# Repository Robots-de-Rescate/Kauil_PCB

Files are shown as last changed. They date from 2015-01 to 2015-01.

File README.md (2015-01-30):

This repository contains the design files for the PCB found on Kauil. The main motivation behind the desigh of this PCB is to have a platform for testing and implementing new hardware easily. Also it should be easy for new students joining the team to start developing for it, this is why we choosed to use the same development board as a core as the one used in the microcontroller (embedded systems) class, the [STM32F3 discovery](http://www.st.com/web/catalog/tools/FM116/SC959/SS1532/PF254044).

The design files were made using [DipTrace](http://diptrace.com/) which can be downloaded freely for 30 days, or without time limitations but with a 300 pin limitation (this design contains more than 300 pins).

## Design of the PCB

The board is for the most part an interface to the various peripherals available on the STM32F3 microcontroller,
but there are also some specific functionalities that should be noted, the is a summary of what the PCB has:

+ Specific purpose connectors, 2 for the MD03 boards and 2 for the encoders. 
+ Driver circuit for a Buzzer to serve as a low battery alert.
+ Driver circuit to read a button so it can be used as an emergency stop. 
+ Analog multiplexer with a voltage divider to measure the voltage of all 5 batteries connected, plus 2 optional
  external signals while using just one ADC.
+ 4 SPI connectors (2 of them 5V tolerant), two connectors per SPI peripheral from the microcontroller with the
  use of CS pins.
+ 4 I2C external connectors, one pair per I2C peripheral on the microcontroller. 2 of them are pulled up to 3.3V
  while the other two are pulled up to 5V.
+ USB communication directly from the microcontroller.
+ One connector for an I2C to USB interface in case communications get saturated over the microcontroler's USB 
  port.
+ 3D gyroscope, 3D magnetometer and 3D accelerometer provided by the STM32F3 discovery board.
+ 5 UART ports (4 of them 5V tolerant)
+ 4 ADC pins exposed to connectors to sense data from various sources.
+ All UART, I2C and SPI connectors have GND and power pins according to the supported voltage to ease the 
  connection of devices with just one connector and one cable.
+ Almost any pin can be set to be a GPIO pin if its specific functionality is not required.

The following diagram shows which pins from the microcontroller are connected to which components on the board,
it's also important to note the red ports that mark issues found while using the board and how they were fixed,
for more information on these see [Known-issues](#known-issues).

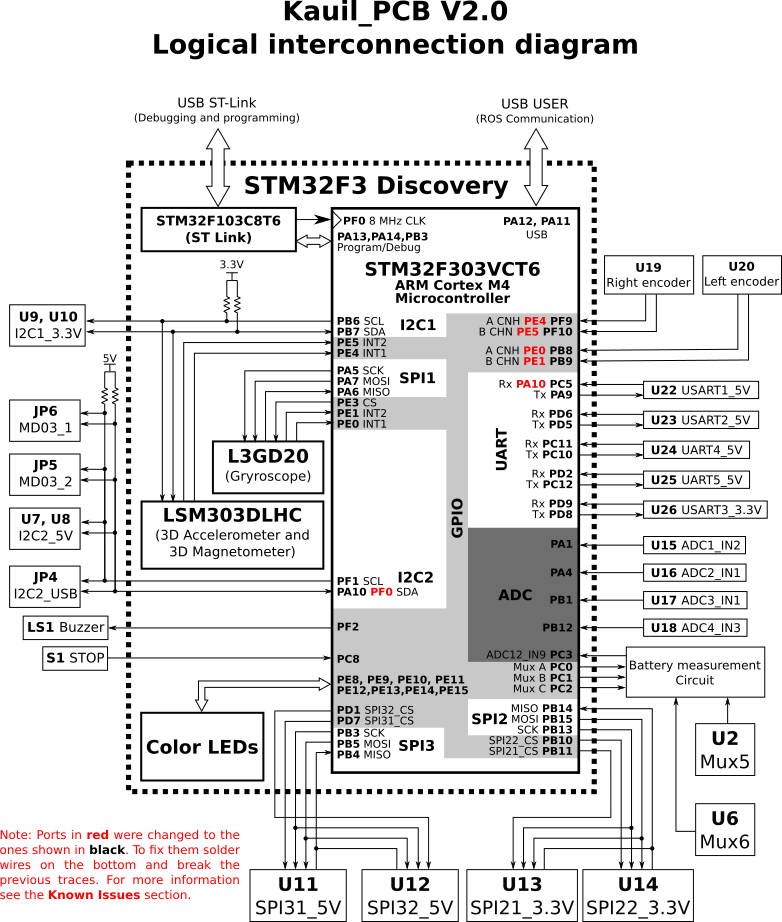
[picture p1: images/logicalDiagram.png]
Logic diagram
  
[PDF version](images/logicalDiagram.pdf)  
[Inkscape's svg version](images/logicalDiagram.svg)

The next diagram shows how the Power sources are distributed within the PCB, care was taken to separate the
regulators that power up the cameras because they are the components that consume the most power (after the CPU
which does not appear in the diagram because it has its own battery and is connected directly).

Note: We've noticed that sometimes when connecting the battery to the regulator in which the Hokuyo is connected 
the regulator shuts down maybe due to a high peak current at startup, most of the times disconnecting and
connecting the battery again fixes this.

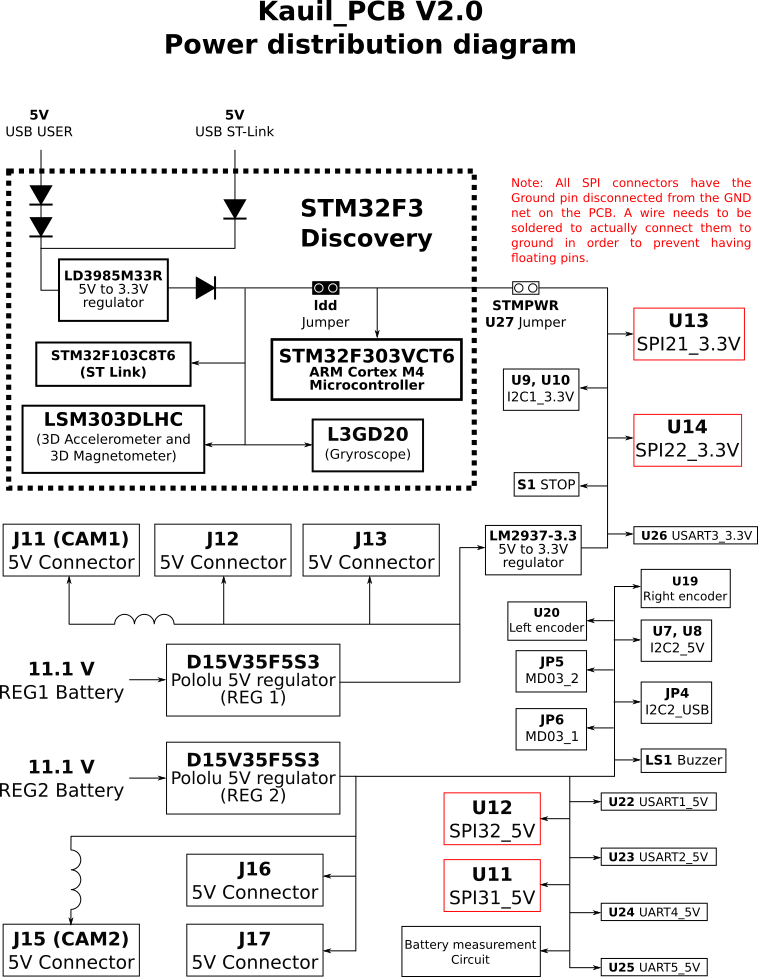
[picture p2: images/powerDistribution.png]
Power distribution
  
[PDF version](images/powerDistribution.pdf)  
[Inkscape's svg version](images/powerDistribution.svg)

To modify any of these diagrams clone the repository, edit the svg file locally with
[Inkscape](https://inkscape.org/), update the png and pdf versions and commit the changes.

## Content of the repository

+ **BOM:** This folder contains some spreadsheets with components used for the PCB, costs and suplier links.
+ **Gerbers:** This folder contains the files that were sent to the manufacturer to produce the actual PCB, they were exported from DipTrace.
+ **Lib:** This folder contains library files for DipTrace with all schematic components and PCB patterns used on the PCB, we do not use any external library besides the one provided by DipTrace and the ones found here, so the design is portable.
+ **PCB.dip:** A DipTrace file with the PCB layout and routing.
+ **PCB.jpg:** A .jpg image of the PCB for quick reference without requiring DipTrace
+ **Schematic.dch:** A DipTrace file with the schematic for the PCB, it contains information about logical connections of the board.
+ **Schematic.jpg:** A .jpg image with the schematics used for the PCB, for easy acces for people that do not have DipTrace.

## Known issues:

V2 of the PCB is the one that was manufactured and is found on Kauil, while doing the code implementation of it we found several problems with the design that had to be corrected for the system to work, the following list explains them, and the fix that was applied, future versions of the board should have them permanently fixed.

* The SDA pin from I2C2 (Used for the MD03 boards) was previously located
  on pin PF0, but this pin is occupied by an 8MHz clock signal that comes
  from the STLink microcontroller on the STM32F3 discovery (U2) and can't
  be changed without slowing down the main microcontroller (the actual
  PF0 pin on the header of the Discovery board is not connected to the 
  microcontroller, and has to be enabled by the SB12 jumper). To fix this 
  the PCB was modified to connect what came into PF0 before to PA10, this 
  pin was the Rx pin for USART1 before, but if required it can be assigned 
  to PC5 which is used for the STLink but suldn't be much trouble while 
  running code (because STLink is just used for programming and debugging), 
  it's important to note that this last jumper wire hasn't been soldered yet.  
  (**Peripherals affected:** I2C2 (MD03), USART1 (Rx pin) )

* The A and B channels for both encoders were assigned incorrectly to pins
  on the STM32F3 that were being already used for interrupts on the two
  sensor chips the LSM303DLHC and the L3GD20, to leave these pins free 
  for future use we chose to move the encoders to other pins, changes made
  were:

      PE4 -> PF9
      PE5 -> PF10
      PE0 -> PB8
      PE1 -> PB9

  (**Periherals affected:** Encoders and external interrupts for sensors 
   LSM303DLHC and the L3GD20)

* The PCB has 4 SPI external connectors, the connector is supposed to 
  provide Ground and Voltage pins to easily connect any device to them,
  but sadly when the schematic was created the Ground pins were left
  unconnected to the actual ground trace. To fix this a wire has to be
  soldered on the bottom of the PCB so the ground is correctly connected.  
  (**Peripherals affected:** all SPI external connectors)

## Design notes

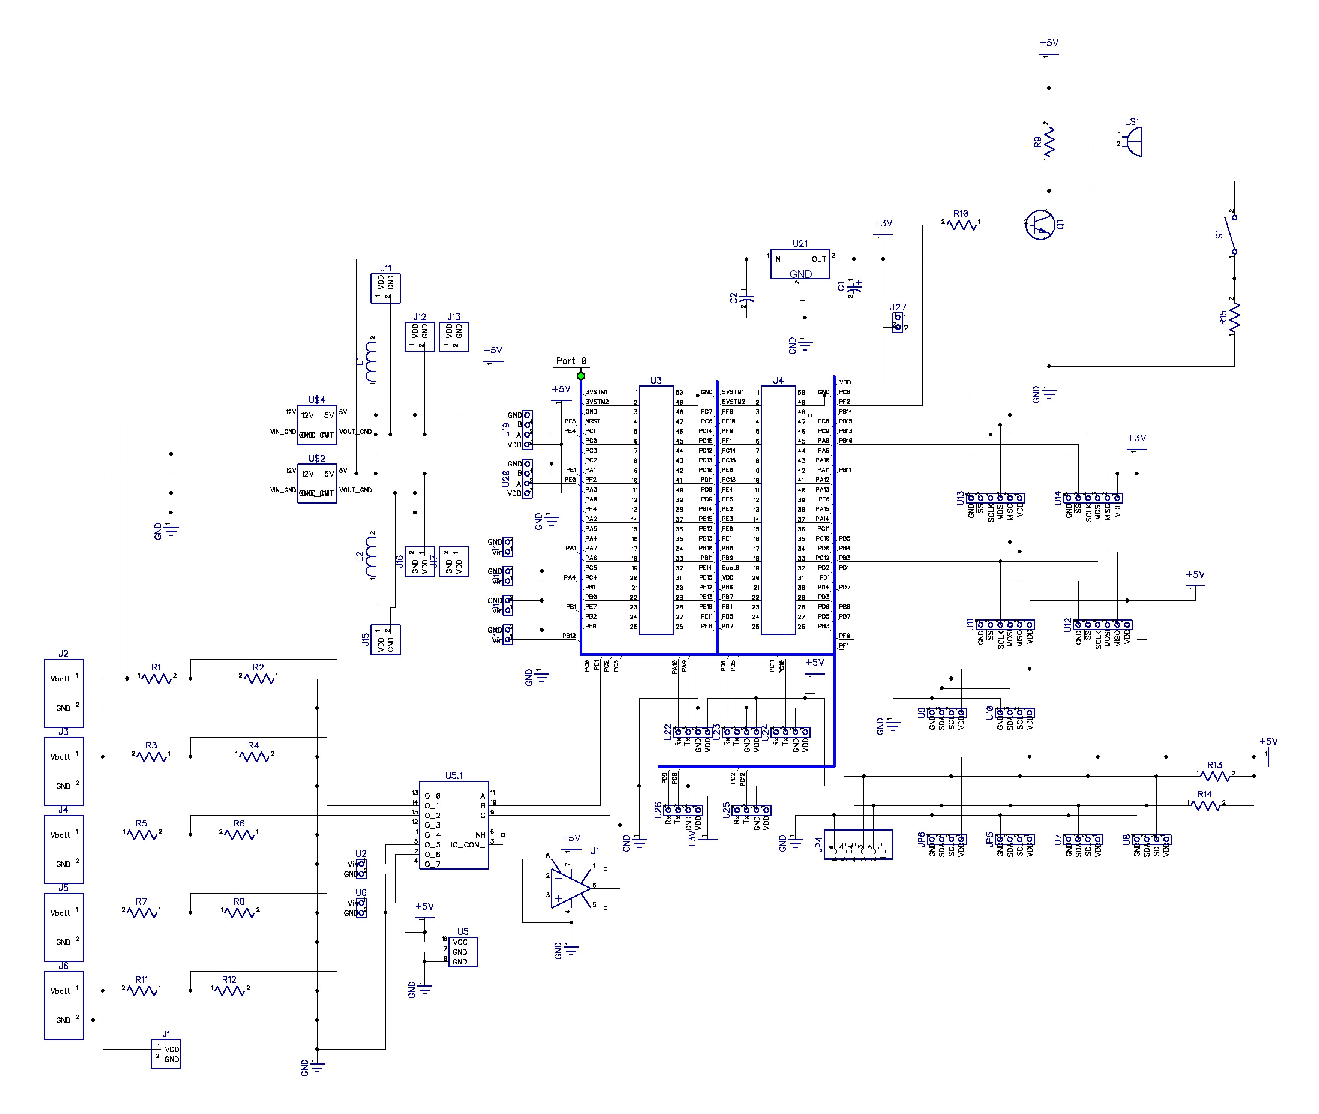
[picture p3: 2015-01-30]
Schematic.jpg

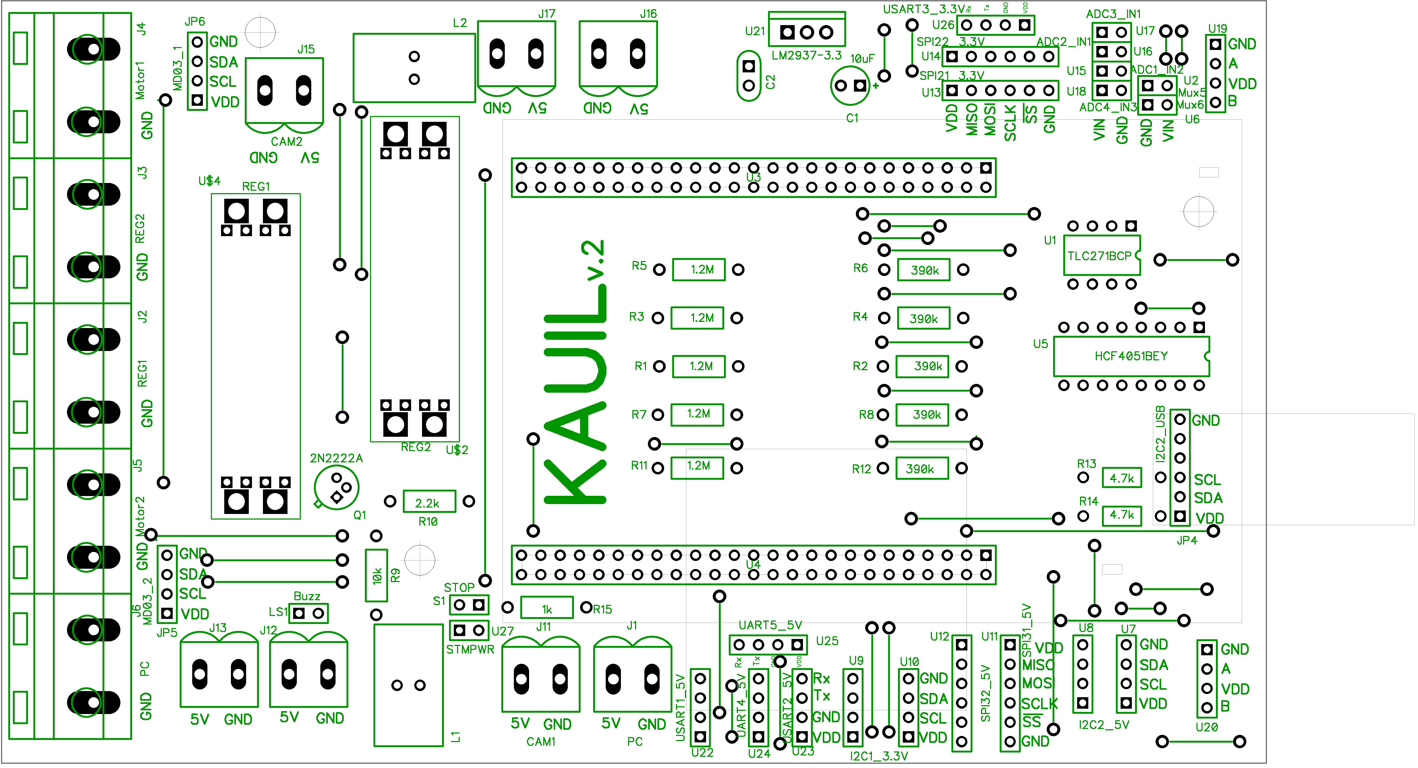
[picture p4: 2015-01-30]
PCB.jpg

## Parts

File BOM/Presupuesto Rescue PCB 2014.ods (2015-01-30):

PRESUPUESTO DE RESCUE 2014
 | Departamento: | Mecatrónica
 | Elaboró: | Santiago León Ortiz
 | Ext:
 | Cotización del dólar: | 13.3733
CANT. | DESCRIPCIÓN | MARCA | MODELO (Número de Parte) | PROVEDOR | OBSERVACIONES | P.UNIT DOLLAR | P. UNIT. M.N. | TOTAL DOLLAR | TOTAL M.N. | Forma de Pago
2 | Regulador de voltaje | Pololu | D15V35F5S3 | Robodacta | Precio en pesos mexicanos |  | 260.00 |  | 520.00 | Tarjeta de crédito o efectivo en la sucursal Lindavista
8 | Bornera pequeña | Weidmuller | BLZ 5.08/2 | Newark Mexico | Precio en dolares | 2.05 | 27.415265 | 16.4 | 219.32212 | Tarjeta de crédito a través de la siguiente página de internet, http://mexico.newark.com/weidmuller/blz-5-08-2/terminal-block-pluggable-2pos/dp/87K2572
7 | Base para bornera pequeña | Weidmuller | SL 5.08 | Newark Mexico | Precio en dolares | 0.817 | 10.9259861 | 5.719 | 76.4819027 | Tarjeta de crédito a través de la siguiente página de internet,http://mexico.newark.com/weidmuller/1517260000/connector-header-5-08mm-2pos/dp/61K5021
5 | Bornera grande | Phoenix Contacts | 1902547 | Mouser Electronics | Precio en dolares | 1.79 | 23.938207 | 8.95 | 119.691035 | Compra en línea a través de la página: http://mx.mouser.com/ProductDetail/Phoenix-Contact/1902547/
1 | Piezo Buzzer | Kobitone | 254-35C5-ROX | Newark Mexico | Precio en dolares | 2.8 | 37.44524 | 2.8 | 37.44524 | Compra en línea a través de la página: http://mx.mouser.com/ProductDetail/Kobitone/254-35C5-ROX/?qs=sGAEpiMZZMtRKYjLzIsEJRPWyohHAawm
20 | Resistencia | KOA speer | MF1/4DCT52R1204F | Mouser Electronics | Precio en dolares | 0.078 | 1.0431174 | 1.56 | 20.862348 | Compra en línea a través de la página: http://mx.mouser.com/ProductDetail/Kobitone/254-35C5-ROX/?qs=sGAEpiMZZMtRKYjLzIsEJRPWyohHAawm
2 | Headers hembra | TE – Conectivity | 2-215309-5 | Mouser Electronics | Precio en dolares | 5.38 | 71.948354 | 10.76 | 143.896708 | Compra en línea a través de la página:http://mx.mouser.com/ProductDetail/TE-Connectivity-AMP/2-215309-5/
2 | Anillo de ferrita | Kemet Nec Tokin | ESD-R-14C-2 | Mouser Electronics | Precio en dolares | 0.338 | 4.5201754 | 0.676 | 9.0403508 | Compra en línea a través de la página: http://mx.mouser.com/ProductDetail/KEMET-NEC-TOKIN/ESD-R-14C-2/?qs=sGAEpiMZZMul3u5M2kZC5JcTFdIfb3Lw
5 | Headers hembra 4 pines | Molex | 90147-1103 | Mouser Electronics | Precio en dolares | 1.61 | 21.531013 | 8.05 | 107.655065 | Compra en línea a través de la página:http://mx.mouser.com/ProductDetail/Molex/90147-1104/
3 | Tira de pines | Molex | 90120-0160 | Mouser Electronics | Precio en dolares | 3.78 | 50.551074 | 11.34 | 151.653222 | Compra en línea a través de la página:http://mx.mouser.com/ProductDetail/Molex/90120-0160/
1 | Transistor NPN | Central Semiconductor | 2N2222A | Mouser Electronics | Precio en dolares | 4.78 | 63.924374 | 4.78 | 63.924374 | Compra en línea a través de la página:http://mx.mouser.com/ProductDetail/Central-Semiconductor/2N2222A/?qs=sGAEpiMZZMutncetXCRkfm67%2fG59BKhz
1 | Regulador de voltaje lineal | Texas Instruments | LM2937ET-3.3/NOPB | Mouser Electronics | Precio en dolares | 2.12 | 28.351396 | 2.12 | 28.351396 | Compra en línea a través de la página: http://mx.mouser.com/ProductDetail/Texas-Instruments/LM2937ET-33-NOPB/
1 | Interfaz USB-Serial | Waveshare | PL2303 USB UART Board | Waveshare | Precio en dolares | 3.99 | 53.359467 | 3.99 | 53.359467 | Compra en línea a través de la página: http://www.wvshare.com/product/PL2303-USB-UART-Board-mini.htm
1 | STM32F3 | ST electronics | STM32F3 Discovery | Mouser Electronics | Precio en dolares | 14.17 | 189.499661 | 14.17 | 189.499661 | Compra en línea a través de la página: http://mx.mouser.com/ProductDetail/Texas-Instruments/LM2937ET-33-NOPB/
 |  |  |  |  |  |  |  | TOTAL M.N. | 1741.1828895

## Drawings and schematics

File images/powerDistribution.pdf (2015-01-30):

# STM32F3

# Kauil_PCB V2.0

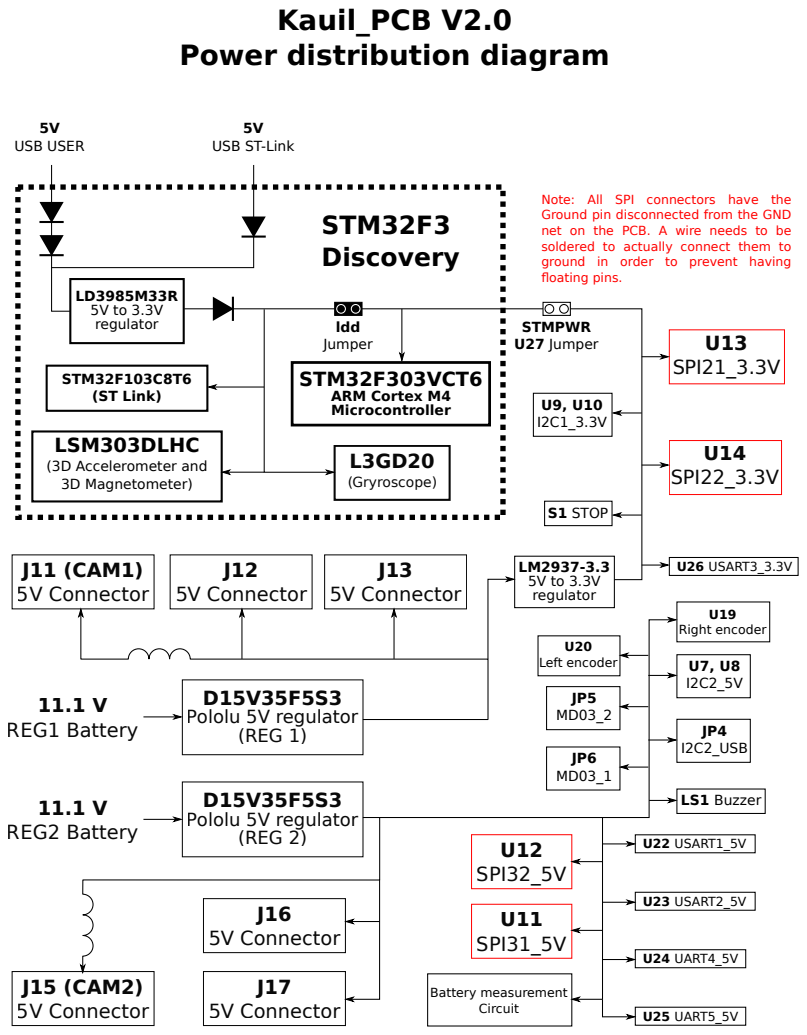
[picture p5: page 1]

Note: All SPI connectors have the
Ground pin disconnected from the GND
net on the PCB. A wire needs to be
soldered to actually connect them to
ground in order to prevent having
floating pins.

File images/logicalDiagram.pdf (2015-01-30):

# STM32F3 Discovery

# Kauil_PCB V2.0

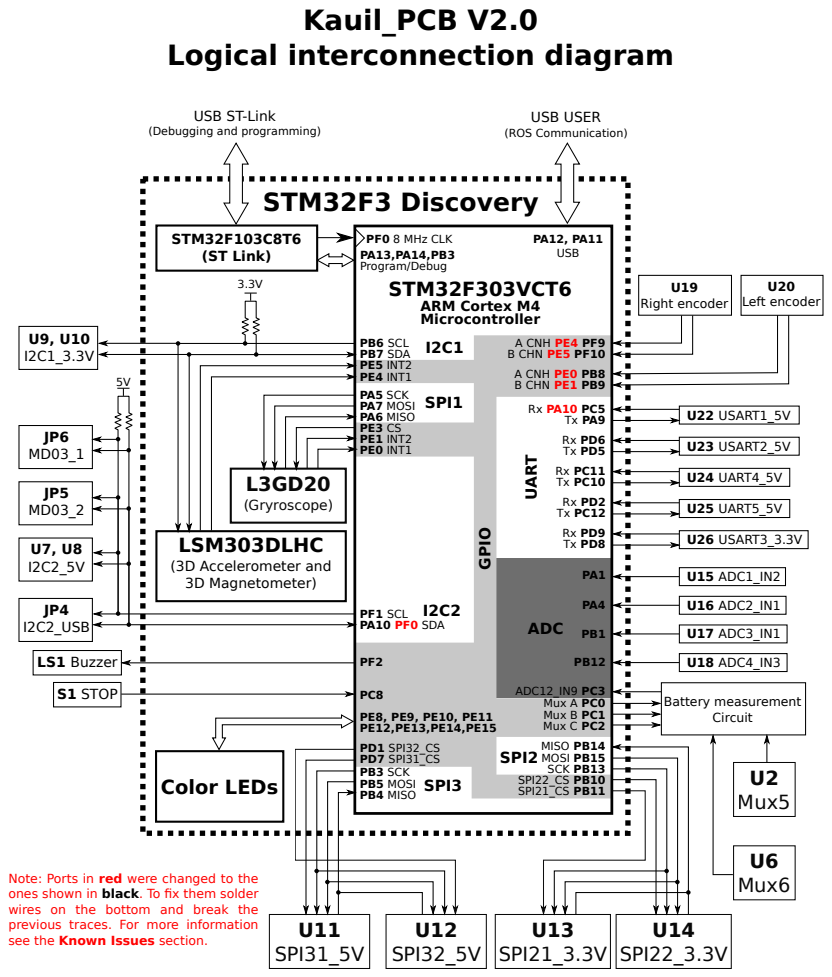
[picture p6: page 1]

Logical interconnection diagram GPIO

Mux6 Note: Ports in red were changed to the
ones shown in black. To fix them solder
wires on the bottom and break the
previous traces. For more information
see the Known Issues section.

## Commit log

2013-09-18 Subiendo archivos de la version 1
    [Board.gbr, BoardOutline.gbr, Bottom.gbr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]
2014-08-10 version 2 del PCB en diptrace
    [Board.gbr, BoardOutline.gbr, Bottom.gbr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]
2015-01-25 Adding a README.md file describing issues with the board
2015-01-30 Adding updated, digital diagrams
    Changing photo of the Logic diagram with a digital version that
    is up to date and also contains the fixes made to solve the issues
    found while programming.
    Adding a diagram that describes how power is distributed through
    the PCB.
2015-01-30 renaming Schematic file
2015-01-30 Adding a jpg image of the schematic
2015-01-30 Adding annotations to PCB, changing preview format from pdf to jpg and update preview PCB.jpg to contain annotations too.
2015-01-30 Connecting explicitly power of U9 and U10 and not by name
2015-01-30 Fixing BOM and removing unnecessary files from the folder
    [Presupuesto Recue 2014.xlsx, Presupuesto Rescue PCB 2014.ods, Presupuesto Rescue PCB 2014.xlsx]
2015-01-30 Changing an issue on README because it was actually ok
    The previous 3rd issue on the README wasn't actually an issue, wires were just connected by name and not explicitly,
    but while checking this, I found actually all ground pins of SPI connectors are floating and not connected to the GND net,
    so I created a new issue explaining this. Also some minor grammar fixes.
2015-01-30 Updating the power diagram to show the correct issue
    The power distribution diagram had an issue that wasn't really
    an issue and didn't had one that was an actual problem.
